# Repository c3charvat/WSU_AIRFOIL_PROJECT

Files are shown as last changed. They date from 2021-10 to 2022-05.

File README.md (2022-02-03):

# WRIGHT STATE DUAL AIRFOIL PROJECT
Source code for the WSU Dual Airfoil Senior Design project.
# Problem Statement:
Wright State graduate and undergraduate students would like to research\
the affects of dual airfoils on lift and pressure.\
The current set up for this system enables the user to set the angle\
of attack (AoA) on each of the airfoils as well as set gap and stagger between them.\
The gap and stagger motion is provided by electrical actuators moving on plastic \
linear berrings driven by a Texas Instruments DAQ. Programed in LabVIEW.\
The AoA was set manual via an arbitrary sharpy scale on a mental plate.

This presented three major issues:\
Year to year no one could actually program, or control this system.\
This system proved to be non-repeatable. (A fundemtal characteristic of an experiment)\
Friction / system stiffness of the linear berrings further reduced the repeatability.\
Using an arbitrary scale made the system qualitative.

# Key project objectives:
*Document all decisions, reasoning, choices, code and files for year to year use.\
*Enable repeatability with a resolution of .1mm gap and stagger and .05* AoA.\
*Use readily available parts to enable maintenance and keep the price down.

The function of this project is to drive 5 steppers in the desired modes.\
They are:\
LCD static- Motor move as soon as data is available from LCD\
LCD Trigger - Motors wait on a "go" button to be pressed in the LCD\
LCD W. Ext. T. - Motors wait on external physical trigger.\
Serial - motors move as soon as serial data is a available.\
Serial W. Ext. T. - Motors move on the press of an physical switch.

# Key features:
Custom G code implementation.\
Implemtiaton of Uart stepper control.\
Native 256 and interpolated 256 micro stepping capable.\
Selectable Spread Cycle or Silent Steptick enabled.\
Low cost use of a 3d printer motherboard.\
Written in Arduino for ease of use for non code centered users.\
PlatformIO configured with nessary libraries provided.\
(For year to year support of Senior design teams).\
(remember to change the path of the libraries in platform.ini)\
Full LCD implementation using SPI.\
Full System UI, with user input enabled through an encoder.\
Prosessor and IDE:\
ARM Stm32f446ZE Branch with Custom PlatformIO implantation.
Black magic probe debugging enabled.\

# Written by:
Collin C. Charvat\
charvat.3@wright.edu\
c3charvat@gmail.com\
B.S. Mechanical Engineering, Wright State University. 22'\
College of Engineering and Computer Science.

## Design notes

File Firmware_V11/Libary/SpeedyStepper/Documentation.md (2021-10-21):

# SpeedyStepper:

This Arduino library is used to control one or more stepper motors.  The motors are accelerated and decelerated as they travel to their destination.  The library has been optimized for speed.

##### Stepper Motor Driver Boards:

SpeedyStepper requires that your stepper motor be connected to the Arduino using drive electronics having a "Step and Direction" interface.  For a hookup guide, go to:
     https://github.com/Stan-Reifel/SpeedyStepper

Examples of Stepper Motor Driver Boards are:

  Pololu's DRV8825 Stepper Motor Driver Carrier:
      https://www.pololu.com/product/2133

  Pololu's A4988 Stepper Motor Driver Carrier:
      https://www.pololu.com/product/2980

  Sparkfun's Big Easy Driver:
      https://www.sparkfun.com/products/12859

  GeckoDrive G203V industrial controller:
      https://www.geckodrive.com/g203v.html

For all driver boards, it is VERY important that you set the motor current.  This is typically done by adjusting a potentiometer on the board.  Read the driver board's documentation to learn how.

##### Selecting a power supply:

Stepper motors will spin with greatest torque at speed, when using a power supply voltage that is many times higher than the motor's voltage rating.  Don't worry about this, the current setting on the driver board keeps the motor protected.  I often use NEMA 17 motors with a voltage rating around 3V, then power my driver board with a 24V supply.  Just make sure that your power supply voltage does not exceed the voltage rating of the driver board.  12V motors with a 12V supply will have much lower torque than my 3V/24V combo.  (Note: NEMA 17 describes the size of the motor, 1.7 inches wide)

Smaller motors can typically spin faster than larger ones.  The best way to evaluate a motor is by looking at its "torque curve".  Most of the stepper motors sold by www.pololu.com have a data sheet on their website 
showing a torque curve (motors sold on Amazon usually do not).

##### Microsteps:

Most stepper motors have a 1.8 degree step angle, which results in 200 steps/revolution.  A typical *Stepper Motor Driver Board* allows you to configure it for Microstepping.  Microstepping gives you greater angular resolution and smoother rotates.  If your board is setup for 2x microstepping, then you will need to move 400 steps for one rotation.  Using 8x microstepping requires 1600 steps / revolution.

##### SpeedyStepper vs FlexyStepper:

A limitation of this library is that once a motion starts, you can not change the target position, speed or rate of acceleration until the motion has completed. The only exception to this is that you can issue a "Stop" at any point in time, which will cause the motor to decelerate to a stop.  The *FlexyStepper* library allows you to make changes in motion.  See:  https://github.com/Stan-Reifel/FlexyStepper

##### The advantage of SpeedyStepper:

Because this library doesn't allow making changes while moving, it can generate steps faster than FlexyStepper.  SpeedyStepper can generate a maximum of about 12,500 steps per second using an Arduino Uno.  Assuming a system driving only one motor at a time, no microstepping, using a 200 steps/rotation motor, the maximum speed is about 62 RPS or 3750 RPM (most stepper motor can not go this fast).  Driving one motor in half step mode, a maximum speed of 31 RPS or 1875 RPM can be reached.  In quarter step mode about 15 RPS or 937 RPM.  Running multiple motors at the same time will reduce the maximum speed.  For example running two motors will reduce the step rate by half or more.

##### Absolute vs relative moves:

The SpeedyStepper functions that make a motor move come in two flavors: *Absolute* and *Relative*.  Relative moves will use a coordinate system that is relative to the motor's current position.  For example moving relative 200 steps, then another 200, then another 200, will turn 600 steps in total (and end up at an absolute position of 600).

Absolute moves use a coordinate system that is referenced to the original position of the motor when it is first turned on.  First issuing an absolute move to position 200 will rotate forward one rotation.  Then running the next absolute move to position 400 will turn just one more revolution in the same direction.  Finally, an absolute move to position 0 will rotate backward two revolutions, back to the starting point.

##### Units of travel:

Frequently issuing move commands in units of "Steps" is not as intuitive as other units, such as *Millimeters* or *Rotations*.  Many stepper motors are used in projects where the motions are linear instead of rotational.  Examples are XY mechanisms such as plotters and 3D printers.  In these cases issuing move commands in Millimeters is much more intuitive than Steps. 

If you choose to work in units of Rotations, you will first need tell the library "how many steps makes one rotation".  Do so using the function:  *setStepsPerRevolution()*.  Then move the motor with calls to *moveToPositionInRevolutions()*  and  *moveRelativeInRevolutions()*.

If you choose to work in units of Millimeters, you will need tell the library "how many steps makes one millimeter".  Do so using the function:  *setStepsPerMillimeter()*.  Then move the motor with calls to *moveToPositionInMillimeters()*  and  *moveRelativeInMillimeters()*.

##### Blocking vs Non-blocking function calls:

The easiest way to tell a stepper motor to move is using a function like this:
	moveToPositionInSteps(125)

This function will rotate the motor until it gets to coordinate 125, but the function call doesn't return until the motion is complete.  This is a *Blocking* function.

Blocking functions are a limitation if you want to do other things while the motor is running.  Examples of "other things" might be to:  1) Run two motors at once.  2) Check if a button is press, then decelerate to a stop.  3) Turn on a solenoid when the motor moves past position 850.  4) Flash a strobe every 200 steps.  5) Run continuously as long as a temperature is below 125 degrees.  To do these types of things *Non-blocking* functions are used.  Here is an example:

```
  //
  // setup the motor so that it will rotate 2000 steps, note: this 
  // command does not start moving yet
  //
  stepper.setupMoveInSteps(2000);
  
  //
  // now execute the move, looping until the motor has finished
  //
  while(!stepper.motionComplete())
  {
    stepper.processMovement();       // this call moves themotor
    
    //
    // check if motor has moved past position 400, if so turn On the LED
    //
    if (stepper.getCurrentPositionInSteps() == 400)
      digitalWrite(LED_PIN, HIGH);
  }
```

There are some limitations to consider:

1. The code that you run while the stepper is moving needs to execute VERY fast.  Perhaps no longer than 0.05 milliseconds.  
2. The only change that you can make to a motion once it starts moving is to decelerate to a stop using *setupStop()*.  Note: This library does not allow changing the target position or speed while the motor is moving.  (You CAN make these changes in FlexyStepper library.

##### Homing:

Many stepper motor projects need to move to exact positions.  This usually requires that the stepper motor library knows where the motor is before it makes its first move.  To achieve this automatically, you will use a 
*Limit Switch* that is pressed by the mechanism when the motor moves all-the-way to one end of its travel.  This procedure called *Homing*, is executed when power is first applied.  A homing program moves the motor toward the limit switch until the switch is pressed, then resets the library so that the motor is now at position 0.

Home automatically is easily done using one of these functions:

- moveToHomeInSteps()
- moveToHomeInRevolutions()
- moveToHomeInMillimeters()

### Usage examples:

```
Near the top of the program, add:
    include "SpeedyStepper.h"

For each stepper, declare a global object outside of all functions as follows:
    SpeedyStepper stepper1;
    SpeedyStepper stepper2;

In Setup(), assign IO pins used for Step and Direction:
    stepper1.connectToPins(10, 11);
    stepper2.connectToPins(12, 14);
```

    Move one motor in units of steps:
        //
        // set the speed in steps/second and acceleration in steps/second/second
        //
        stepper1.setSpeedInStepsPerSecond(100);
        stepper1.setAccelerationInStepsPerSecondPerSecond(100);
    
        //
        // move 200 steps in the backward direction
        //
        stepper1.moveRelativeInSteps(-200);
    
        //
        // move to an absolute position of 200 steps
        //
        stepper1.moveToPositionInSteps(200);

    Move one motor in units of revolutions:
        //
        // set the number of steps per revolutions, 200 with no microstepping, 
        // 800 with 4x microstepping
        //
        stepper1.setStepsPerRevolution(200);
    
        //
        // set the speed in rotations/second and acceleration in 
        // rotations/second/second
        //
        stepper1.setSpeedInRevolutionsPerSecond(1);
        stepper1.setAccelerationInRevolutionsPerSecondPerSecond(1);
    
        //
        // move backward 1.5 revolutions
        //
        stepper1.moveRelativeInRevolutions(-1.5);
    
        //
        // move to an absolute position of 3.75 revolutions
        //
        stepper1.moveToPositionInRevolutions(3.75);

    Move one motor in units of millimeters:
        //
        // set the number of steps per millimeter
        //
        stepper1.setStepsPerMillimeter(25);
    
        //
        // set the speed in millimeters/second and acceleration in 
        // millimeters/second/second
        //
        stepper1.setSpeedInMillimetersPerSecond(20);
        stepper1.setAccelerationInMillimetersPerSecondPerSecond(20);
    
        //
        // move backward 15.5 millimeters
        //
        stepper1.moveRelativeInMillimeters(-15.5);
    
        //
        // move to an absolute position of 125 millimeters
        //
        stepper1.moveToPositionInMillimeters(125);

    Move two motors in units of revolutions:
        //
        // set the number of steps per revolutions, 200 with no microstepping, 
        // 800 with 4x microstepping
        //
        stepper1.setStepsPerRevolution(200);
        stepper2.setStepsPerRevolution(200);
    
        //
        // set the speed in rotations/second and acceleration in 
        // rotations/second/second
        //
        stepper1.setSpeedInRevolutionsPerSecond(1);
        stepper1.setAccelerationInRevolutionsPerSecondPerSecond(1);
        stepper2.setSpeedInRevolutionsPerSecond(1);
        stepper2.setAccelerationInRevolutionsPerSecondPerSecond(1);
    
        //
        // setup motor 1 to move backward 1.5 revolutions, this step does not 
        // actually move the motor
        //
        stepper1.setupRelativeMoveInRevolutions(-1.5);
    
        //
        // setup motor 2 to move forward 3.0 revolutions, this step does not 
        // actually move the motor
        //
        stepper2.setupRelativeMoveInRevolutions(3.0);
    
        //
        // execute the moves
        //
        while((!stepper1.motionComplete()) || (!stepper2.motionComplete()))
        {
          stepper1.processMovement();
          stepper2.processMovement();
        }

# The library of functions  

### Setup functions: 

```
//
// connect the stepper object to the IO pins
//  Enter:  stepPinNumber = IO pin number for the Step
//          directionPinNumber = IO pin number for the direction bit
//          enablePinNumber = IO pin number for the enable bit (LOW is enabled)
//            set to 0 if enable is not supported
//
void connectToPins(byte stepPinNumber, byte directionPinNumber)
```

### Functions with units in millimeters: 

```
//
// set the number of steps the motor has per millimeter
//
void setStepsPerMillimeter(float motorStepPerMillimeter)

//
// get the current position of the motor in millimeter, this functions is updated
// while the motor moves
//  Exit:  a signed motor position in millimeter returned
//
float getCurrentPositionInMillimeters()

//
// set current position of the motor in millimeter, this does not move the motor
//
void setCurrentPositionInMillimeters(float currentPositionInMillimeter)

//
// set the maximum speed, units in millimeters/second, this is the maximum speed  
// reached while accelerating
// Note: this can only be called when the motor is stopped
//  Enter:  speedInMillimetersPerSecond = speed to accelerate up to, units in 
//          millimeters/second
//
void setSpeedInMillimetersPerSecond(float speedInMillimetersPerSecond)

//
// set the rate of acceleration, units in millimeters/second/second
// Note: this can only be called when the motor is stopped
//  Enter:  accelerationInMillimetersPerSecondPerSecond = rate of acceleration,  
//          units in millimeters/second/second
//
void setAccelerationInMillimetersPerSecondPerSecond(
                      float accelerationInMillimetersPerSecondPerSecond)

//
// home the motor by moving until the homing sensor is activated, then set the  
// position to zero, with units in millimeters
//  Enter:  directionTowardHome = 1 to move in a positive direction, -1 to move in 
//             a negative directions 
//          speedInMillimetersPerSecond = speed to accelerate up to while moving 
//             toward home, units in millimeters/second
//          maxDistanceToMoveInMillimeters = unsigned maximum distance to move 
//             toward home before giving up
//          homeSwitchPin = pin number of the home switch, switch should be 
//             configured to go low when at home
//  Exit:   true returned if successful, else false
//
bool moveToHomeInMillimeters(long directionTowardHome,  
  float speedInMillimetersPerSecond, long maxDistanceToMoveInMillimeters, 
  int homeLimitSwitchPin)

//
// move relative to the current position, units are in millimeters, this function  
// does not return until the move is complete
//  Enter:  distanceToMoveInMillimeters = signed distance to move relative to the  
//          current position in millimeters
//
void moveRelativeInMillimeters(float distanceToMoveInMillimeters)

//
// setup a move relative to the current position, units are in millimeters, no   
// motion occurs until processMove() is called
// Note: this can only be called when the motor is stopped
//  Enter:  distanceToMoveInMillimeters = signed distance to move relative to the  
//            currentposition in millimeters
//
void setupRelativeMoveInMillimeters(float distanceToMoveInMillimeters)

//
// move to the given absolute position, units are in millimeters, this function 
// does not return until the move is complete
//  Enter:  absolutePositionToMoveToInMillimeters = signed absolute position to 
//            move toin units of millimeters
//
void moveToPositionInMillimeters(
                      float absolutePositionToMoveToInMillimeters)

//
// setup a move, units are in millimeters, no motion occurs until processMove() is 
// called.  Note: this can only be called when the motor is stopped
//  Enter:  absolutePositionToMoveToInMillimeters = signed absolute position to move  
//          to in units of millimeters
//
void setupMoveInMillimeters(
                      float absolutePositionToMoveToInMillimeters)

//
// Get the current velocity of the motor in millimeters/second.  This functions is 
// updated while it accelerates up and down in speed.  This is not the desired  
// speed, but the speed the motor should be moving at the time the function is   
// called.  This is a signed value and is negative when motor is moving backwards.
// Note: This speed will be incorrect if the desired velocity is set faster than
// this library can generate steps, or if the load on the motor is too great for
// the amount of torque that it can generate.
//  Exit:  velocity speed in millimeters per second returned, signed
//
float getCurrentVelocityInMillimetersPerSecond()

```

### Functions with units in revolutions: 

```
//
// set the number of steps the motor has per revolution
//
void setStepsPerRevolution(float motorStepPerRevolution)

//
// get the current position of the motor in revolutions, this functions is updated
// while the motor moves
//  Exit:  a signed motor position in revolutions returned
//
float getCurrentPositionInRevolutions()

//
// set current position of the motor in revolutions, this does not move the motor
//
void setCurrentPositionInRevolutions(
   float currentPositionInRevolutions)

//
// set the maximum speed, units in revolutions/second, this is the maximum speed  
// reached while accelerating.  Note: this can only be called when the motor is 
// stopped
//  Enter:  speedInRevolutionsPerSecond = speed to accelerate up to, units in 
//            revolutions/second
//
void setSpeedInRevolutionsPerSecond(float speedInRevolutionsPerSecond)

//
// set the rate of acceleration, units in revolutions/second/second
// Note: this can only be called when the motor is stopped
//  Enter:  accelerationInRevolutionsPerSecondPerSecond = rate of acceleration,  
//            units inrevolutions/second/second
//
void setAccelerationInRevolutionsPerSecondPerSecond(
                      float accelerationInRevolutionsPerSecondPerSecond)

//
// home the motor by moving until the homing sensor is activated, then set the  
// position to zero, with units in revolutions
//  Enter:  directionTowardHome = 1 to move in a positive direction, -1 to move in 
//             a negative directions 
//          speedInRevolutionsPerSecond = speed to accelerate up to while moving 
//             toward home, units in revolutions/second
//          maxDistanceToMoveInRevolutions = unsigned maximum distance to move 
//             toward home before giving up
//          homeSwitchPin = pin number of the home switch, switch should be 
//             configured to go low when at home
//  Exit:   true returned if successful, else false
//
bool moveToHomeInRevolutions(long directionTowardHome, 
  float speedInRevolutionsPerSecond, long maxDistanceToMoveInRevolutions, 
  int homeLimitSwitchPin)

//
// move relative to the current position, units are in revolutions, this function  
// does not return until the move is complete
//  Enter:  distanceToMoveInRevolutions = signed distance to move relative to the  
//          current position in revolutions
//
void moveRelativeInRevolutions(float distanceToMoveInRevolutions)

//
// setup a move relative to the current position, units are in revolutions, no   
// motion occurs until processMove() is called.  Note: this can only be called 
// when the motor is stopped
//  Enter:  distanceToMoveInRevolutions = signed distance to move relative to the  
//          current position in revolutions
//
void setupRelativeMoveInRevolutions(float distanceToMoveInRevolutions)

//
// move to the given absolute position, units are in revolutions, this function 
// does not return until the move is complete
//  Enter:  absolutePositionToMoveToInRevolutions = signed absolute position to  
//          move to in units of revolutions
//
void moveToPositionInRevolutions(
       float absolutePositionToMoveToInRevolutions)

//
// setup a move, units are in revolutions, no motion occurs until processMove() is 
// called.  Note: this can only be called when the motor is stopped
//  Enter:  absolutePositionToMoveToInRevolutions = signed absolute position to  
//          move to inunits of revolutions
//
void setupMoveInRevolutions(
          float absolutePositionToMoveToInRevolutions)

//
// Get the current velocity of the motor in revolutions/second.  This functions is 
// updated while it accelerates up and down in speed.  This is not the desired  
// speed, but the speed the motor should be moving at the time the function is   
// called.  This is a signed value and is negative when motor is moving backwards.
// Note: This speed will be incorrect if the desired velocity is set faster than
// this library can generate steps, or if the load on the motor is too great for
// the amount of torque that it can generate.
//  Exit:  velocity speed in revolutions per second returned, signed
//
float getCurrentVelocityInRevolutionsPerSecond()

```

### Functions with units in steps: 

```
//
// set the current position of the motor in steps, this does not move the motor
// Note: This function should only be called when the motor is stopped
//    Enter:  currentPositionInSteps = the new position of the motor in steps
//
void setCurrentPositionInSteps(long currentPositionInSteps)

//
// get the current position of the motor in steps, this functions is updated
// while the motor moves
//  Exit:  a signed motor position in steps returned
//
long getCurrentPositionInSteps()

//
// setup a "Stop" to begin the process of decelerating from the current velocity to  
// zero, decelerating requires calls to processMove() until the move is complete
// Note: This function can be used to stop a motion initiated in units of steps or 
// revolutions
//
void setupStop()

//
// set the maximum speed, units in steps/second, this is the maximum speed reached  
// while accelerating
// Note: this can only be called when the motor is stopped
//  Enter:  speedInStepsPerSecond = speed to accelerate up to, units in steps/second
//
void setSpeedInStepsPerSecond(float speedInStepsPerSecond)

//
// set the rate of acceleration, units in steps/second/second
// Note: this can only be called when the motor is stopped
//  Enter:  accelerationInStepsPerSecondPerSecond = rate of acceleration, units in 
//          steps/second/second
//
void setAccelerationInStepsPerSecondPerSecond(
                      float accelerationInStepsPerSecondPerSecond)

//
// home the motor by moving until the homing sensor is activated, then set the 
// position to zero with units in steps
//  Enter:  directionTowardHome = 1 to move in a positive direction, -1 to move in 
//             a negative directions 
//          speedInStepsPerSecond = speed to accelerate up to while moving toward 
//             home, units in steps/second
//          maxDistanceToMoveInSteps = unsigned maximum distance to move toward 
//             home before giving up
//          homeSwitchPin = pin number of the home switch, switch should be 
//             configured to go low when at home
//  Exit:   true returned if successful, else false
//
bool moveToHomeInSteps(long directionTowardHome, 
  float speedInStepsPerSecond, long maxDistanceToMoveInSteps, int homeLimitSwitchPin)

//
// move relative to the current position, units are in steps, this function does 
// not return until the move is complete
//  Enter:  distanceToMoveInSteps = signed distance to move relative to the current 
//            position in steps
//
void moveRelativeInSteps(long distanceToMoveInSteps)

//
// setup a move relative to the current position, units are in steps, no motion  
// occurs until processMove() is called.  Note: this can only be called when the 
// motor is stopped
//  Enter:  distanceToMoveInSteps = signed distance to move relative to the current  
//          position in steps
//
void setupRelativeMoveInSteps(long distanceToMoveInSteps)

//
// move to the given absolute position, units are in steps, this function does not 
// return until the move is complete
//  Enter:  absolutePositionToMoveToInSteps = signed absolute position to move to  
//            in units of steps
//
void moveToPositionInSteps(long absolutePositionToMoveToInSteps)

//
// setup a move, units are in steps, no motion occurs until processMove() is called
// Note: this can only be called when the motor is stopped
//  Enter:  absolutePositionToMoveToInSteps = signed absolute position to move to in 
//          units of steps
//
void setupMoveInSteps(long absolutePositionToMoveToInSteps)

//
// if it is time, move one step
//  Exit:  true returned if movement complete, false returned not a final target 
//           position yet
//
bool processMovement(void)

//
// Get the current velocity of the motor in steps/second.  This functions is updated
// while it accelerates up and down in speed.  This is not the desired speed, but  
// the speed the motor should be moving at the time the function is called.  This  
// is a signed value and is negative when the motor is moving backwards.
// Note: This speed will be incorrect if the desired velocity is set faster than
// this library can generate steps, or if the load on the motor is too great for
// the amount of torque that it can generate.
//  Exit:  velocity speed in steps per second returned, signed
//
float getCurrentVelocityInStepsPerSecond()

//
// check if the motor has competed its move to the target position
//  Exit:  true returned if the stepper is at the target position
//
bool motionComplete()

```

Copyright (c) 2018 S. Reifel & Co.  -   Licensed under the MIT license.

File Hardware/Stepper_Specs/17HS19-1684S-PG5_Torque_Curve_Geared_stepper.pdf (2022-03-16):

## MAX. Permissible Torque：2Nm

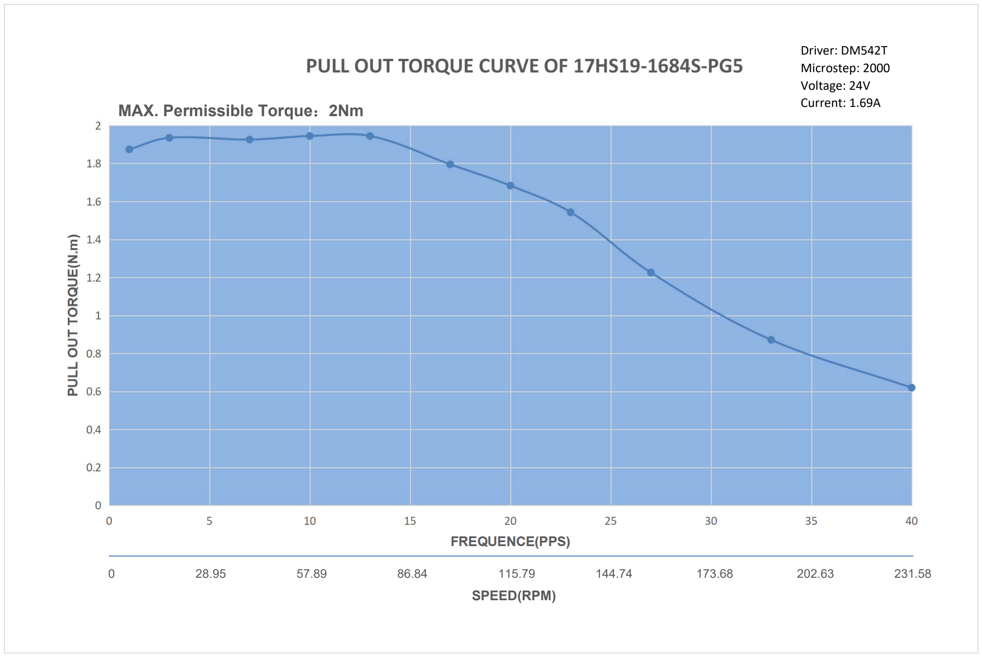
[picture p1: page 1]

SPEED(RPM)

0 | 28.95 | 57.89 | 86.84 | 115.79 | 144.74 | 173.68 | 202.63 | 231.58

Driver: DM542T
Microstep: 2000
Voltage: 24V
Current: 1.69A

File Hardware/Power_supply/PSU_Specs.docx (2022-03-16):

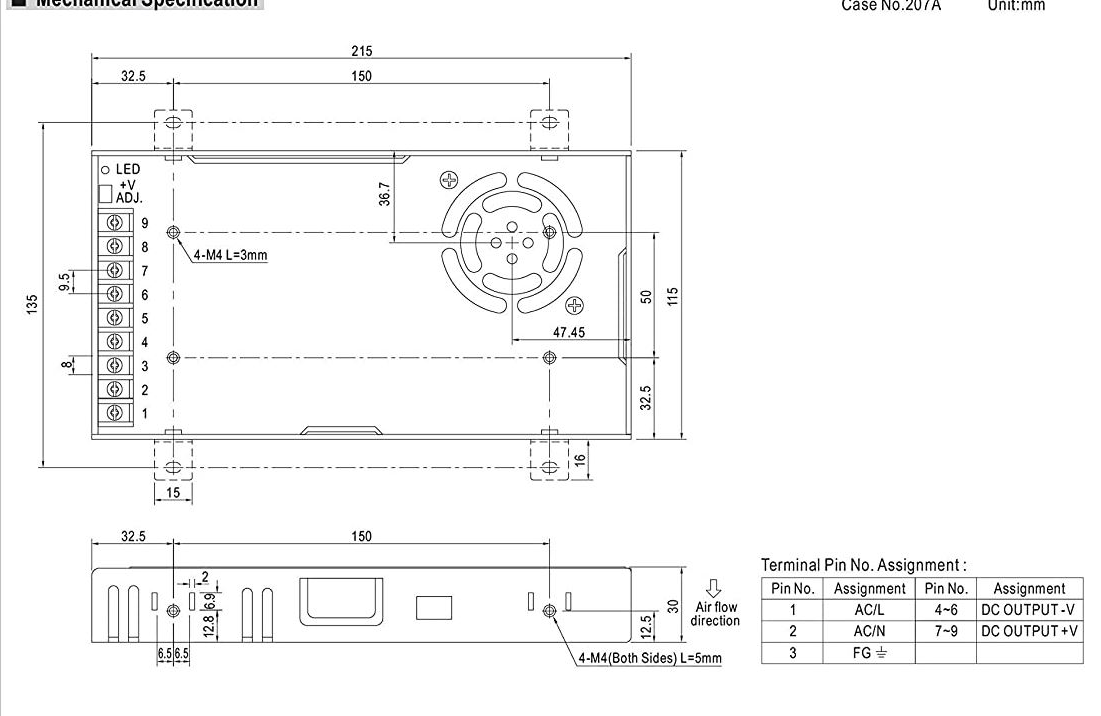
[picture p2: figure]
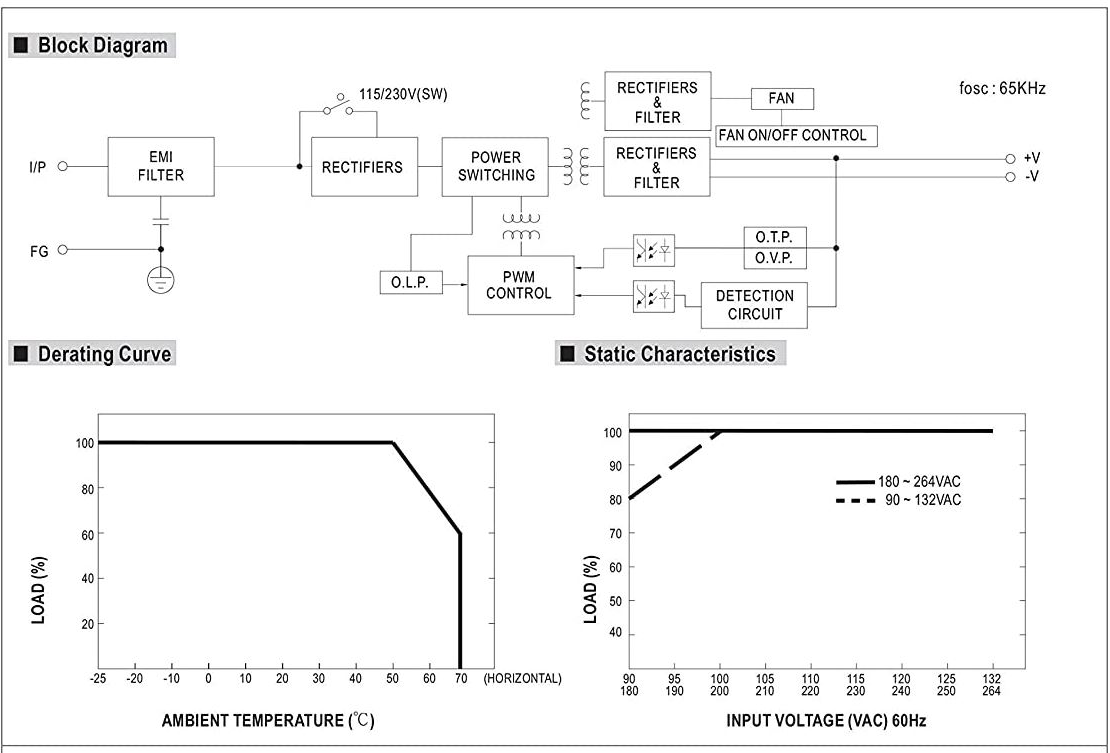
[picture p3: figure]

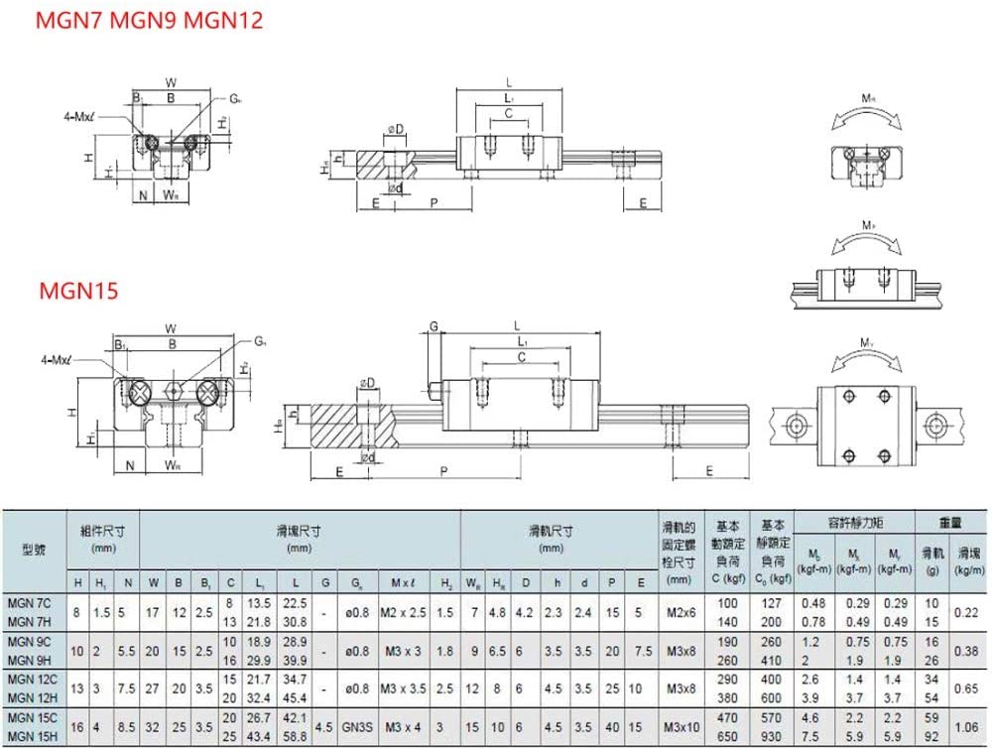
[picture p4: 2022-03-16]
Hardware/Linear_rails/61ZwrpNV6dL._AC_SL1000_.jpg

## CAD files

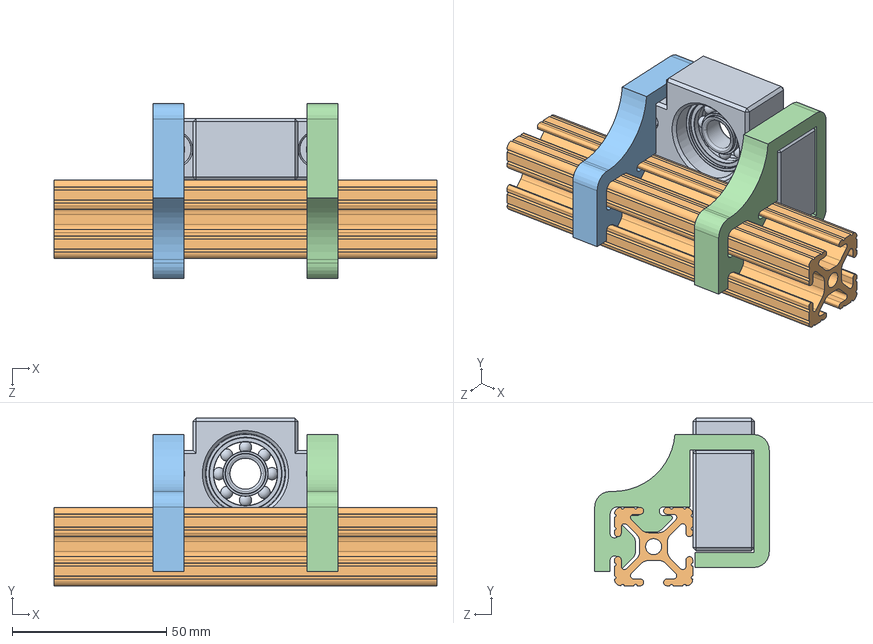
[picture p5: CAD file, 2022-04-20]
CADD/Dual Airfoil/Frame/bf12_to_tslot/bf12_to_tslot_sub_assm.SLDASM
124.2 x 54.4 x 56.6 mm
BF12
47065T121_T-Slotted Framing
bf12_to_tslot_V2_left
bf12_to_tslot_V2_right

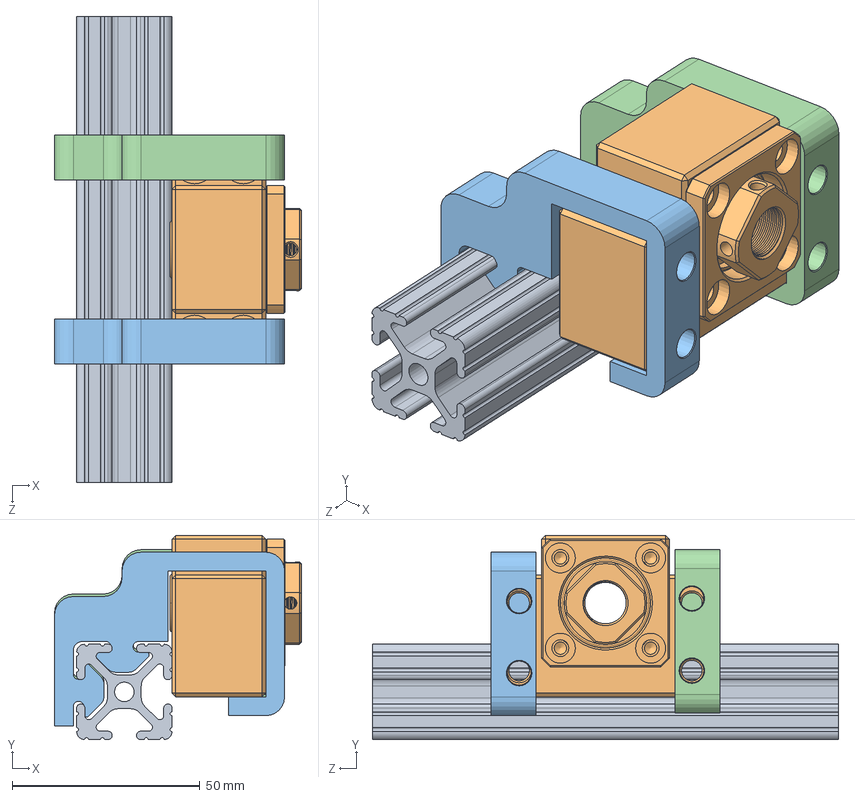
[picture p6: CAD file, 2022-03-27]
CADD/Dual Airfoil/Frame/bk12_to_tslot/bk12_t0_tslot.SLDASM
65.8 x 54.4 x 124.2 mm
47065T121_T-Slotted Framing
BK12
bk12_to_tslot_V1_mirriored
bk12_to_tslot_V1

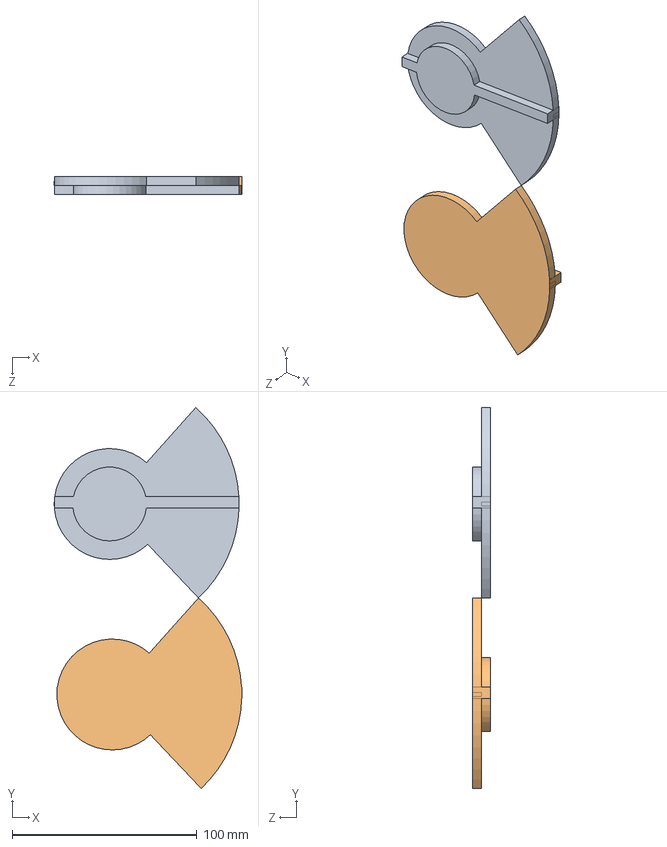
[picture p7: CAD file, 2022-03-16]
CADD/Dual Airfoil/Frame/AoA Slider/Black Plate Alignment.SLDASM
101.5 x 206.2 x 10.0 mm
black plate gap
black plate stagger

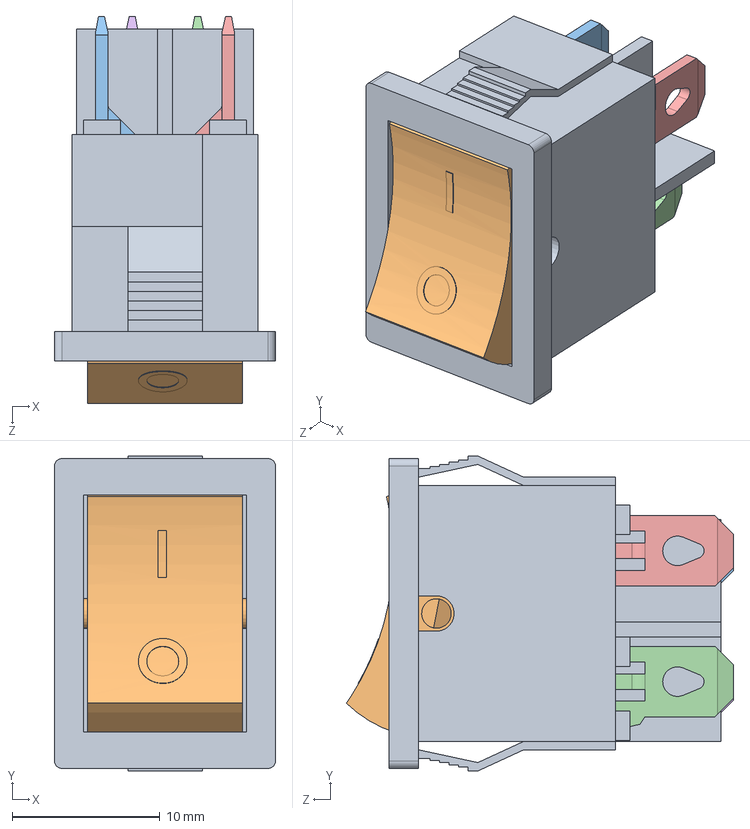
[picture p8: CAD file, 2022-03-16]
CADD/Dual Airfoil/Enclosure_assm/Power_socket/IEC320 C14 Inlet Power Module/switch.SLDASM
14.9 x 21.3 x 26.2 mm
switch_base
rocker
sm_tab_type1a
sm_tab_type1b
sm_tab_type2a
sm_tab_type2b

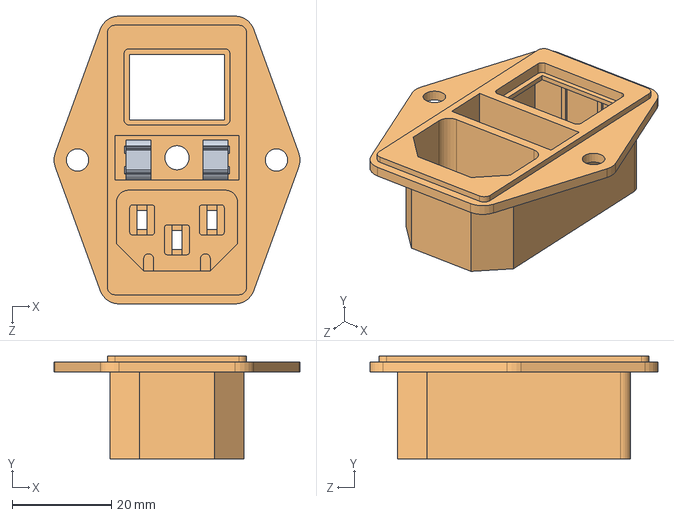
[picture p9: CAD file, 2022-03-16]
CADD/Dual Airfoil/Enclosure_assm/Power_socket/IEC320 C14 Inlet Power Module/IEC320-C14 .SLDASM
49.4 x 20.7 x 57.9 mm
fuse_clip_set
ilpm_case

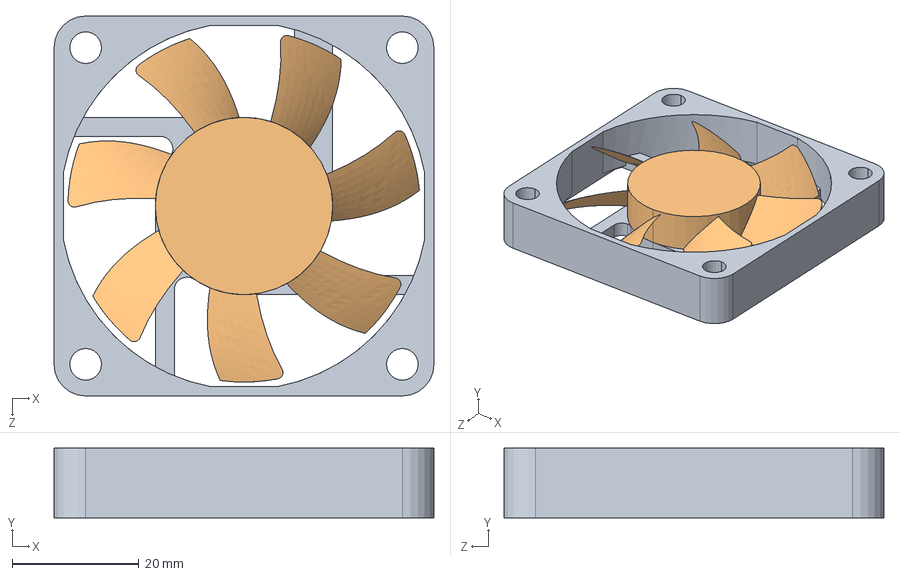
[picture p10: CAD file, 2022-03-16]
CADD/Dual Airfoil/Enclosure_assm/Fan_Assembly.STEP.SLDASM
60.0 x 11.0 x 60.0 mm
Fan_Case___ _________.STEP
Fan___ _________.STEP

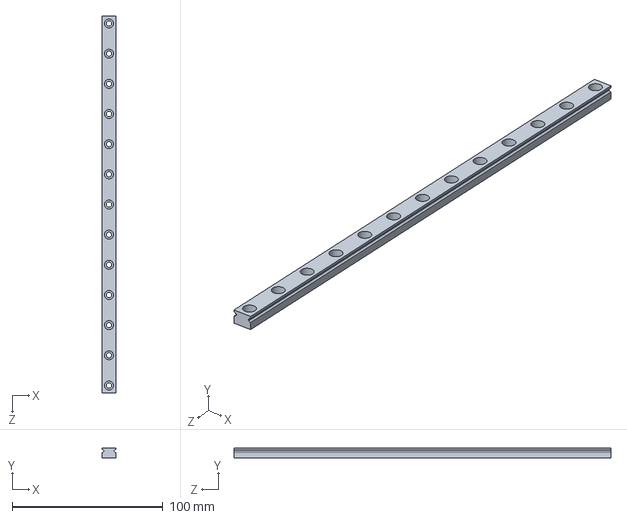
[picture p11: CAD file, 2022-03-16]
CADD/Dual Airfoil/Frame/MGN9.SLDASM
9.00 x 6.50 x 250.0 mm

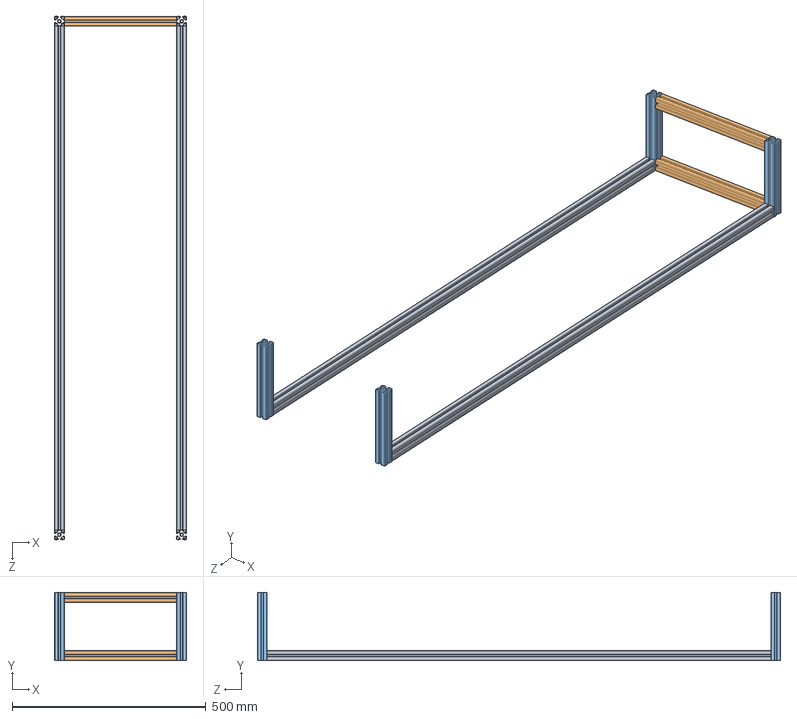
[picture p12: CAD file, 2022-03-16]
CADD/Dual Airfoil/Frame/Stagger Frame.SLDASM
340.8 x 175.8 x 1350.8 mm
Stagger - 1300x x 2
Gap-220z x 2
Stagger 125y x 4

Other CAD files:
CADD/Dual Airfoil/Enclosure_assm/motherboard bs/SIDE_L-1.stp.SLDASM
CADD/Dual Airfoil/Enclosure_assm/motherboard bs/C10.stp.STEP.SLDASM
CADD/Dual Airfoil/Enclosure_assm/motherboard bs/SOT23-5.stp.STEP.SLDASM
CADD/Dual Airfoil/Enclosure_assm/motherboard bs/254-3X4-1.stp.STEP.SLDASM
CADD/Dual Airfoil/Enclosure_assm/motherboard bs/R7.stp.SLDASM
CADD/Dual Airfoil/Enclosure_assm/motherboard bs/2P-254.stp.STEP.SLDASM
CADD/Dual Airfoil/Enclosure_assm/motherboard bs/TSSOP-16.stp.STEP.SLDASM
CADD/Dual Airfoil/Enclosure_assm/motherboard bs/Free-Models.stp.STEP.SLDASM
CADD/Dual Airfoil/Enclosure_assm/motherboard bs/User Library-V0603HD.stp.STEP.SLDASM
CADD/Dual Airfoil/Enclosure_assm/motherboard bs/C5.stp.STEP.SLDASM
CADD/Dual Airfoil/Enclosure_assm/Assem1.SLDASM
CADD/Dual Airfoil/Enclosure_assm/BIGTREETECH Octopus V1.0.stp.SLDASM
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

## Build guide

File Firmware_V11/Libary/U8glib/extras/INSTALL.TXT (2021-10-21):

U8GLIB
http://code.google.com/p/u8glib/

Install instructions for the Arduino environment.

  1. Start Arduino IDE
  2. In the Arduino IDE, import the library from the "Add Library" Menu.

Alternative install instructions for the Arduino environment.

  1. Unzip u8glib_arduino_vX.XX.zip into the "libraries" folder of the
      Arduino install directory
  2. Start Arduino IDE

Install instructions for the Chipkit (Arduino) environment.

  1. cd <mpide-... path>/libraries
  2. unzip u8glib_arduino_vX.XX.zip
  3. cd <mpide-... path>///hardware/pic32/libraries
  4. again: u8glib_arduino_vX.XX.zip
  5. Open hardware/pic32/cores/pic32/Print.h
	  Remove line
	    #define BYTE 0
	  from the file, use PRINT_BYTE instead of BYTE.

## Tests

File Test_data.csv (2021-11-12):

 | x | y | AoA T | AoA B
Scenario0 | 200 | 50 | -10 | 10
Scenario1 | 100 | 60 | 10 | -10
Scenario2 | 0 | 200 | 20 | 15
Scenario3 | 300 | 400 | 10 | 3
Scenario4 | 500 | 500 | 5 | 7
Scenario5 | 10 | 100 | 3 | 10

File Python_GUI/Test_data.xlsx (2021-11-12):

 | Scenario1
x | 20
y | 30
AoA T | 40
AoA B | 200

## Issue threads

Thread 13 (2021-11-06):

Movement bug

c3charvat, 2021-11-06:
Steppers still move after Error message is dismissed.

c3charvat, 2021-11-12:
Fixed by merging the serial and LCD position input variables into one and initializing temp positions. Postion_Data Removed.

Closed 2021-11-12.

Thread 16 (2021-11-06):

Implemtiaton - Hardware reset via software trigger?

c3charvat, 2021-11-06:
Use the exposed software reset pin to reset the board at the request of software in the event of an unrecoverable error.

c3charvat, 2021-11-13:
Implemented <R> Command

Closed 2021-11-13.

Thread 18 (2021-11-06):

Implemtiaton of leadscrew math

c3charvat, 2021-11-06:
X and Y axis need math to go from steps to mm moved. Which is the value the user inputs.

c3charvat, 2021-11-13:
Done

Closed 2021-11-13.

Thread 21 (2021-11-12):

Implement Stop/ Reset

c3charvat, 2021-11-12:
Implement Stop/Reset
For the LCD and for the GUI
This includes:
New Menu for Reset in LCD
Implementing reset Function for the GUI
Adding the reset Function in the g code parser

c3charvat, 2021-11-13:
Done Just Cuts power to the board Via PBO jumped to reset and set high Whenever the <R> code is sent

c3charvat, 2022-02-03:
software reset now implemented with NVIC_SystemReset(). -> only happens during error state

Closed 2022-02-03.

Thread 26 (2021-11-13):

Add Reset To LCD Menus

c3charvat, 2021-11-13:

c3charvat, 2021-11-20:
Reset is going to be handled by a physical switch - Per Discussion on 11/18

Closed 2021-11-20.

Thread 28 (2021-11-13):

Calculate the max distance to home and update the values in the homing function

c3charvat, 2021-11-13:

c3charvat, 2021-11-20:
This function is being replaced entirely, as it only works on a single axis at a time which isnt a good use case for this application as multiple steppers are used per axis -> a new homing function has been written using the move function

Closed 2021-11-20.

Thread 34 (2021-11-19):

X axis not moving ->

c3charvat, 2021-11-19:
Could be the driver?

c3charvat, 2021-11-24:
X axis moved, today, but never stopped and just kept going in circles.

c3charvat, 2021-12-14:
it moves, was an internal issue with the python in the way the movement was calculated

Closed 2021-12-14.

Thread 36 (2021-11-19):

Re-assign Motor Functions so they make sense for the board

c3charvat, 2021-11-19:
motor 2 is doubled
and we need to decide on the assignment of motors

c3charvat, 2021-11-22:
This will be implemented later names are fine for now.

Closed 2021-11-22.

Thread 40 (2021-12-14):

Rewrite and unify all homing functions

c3charvat, 2021-12-14:
Homing functions are a classic example of when we should use a high priority ISR (interrupt) and previously we had been using overloaded variables.

c3charvat, 2021-12-25:
This is done- untested

Closed 2021-12-25.

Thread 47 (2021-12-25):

Reduce the final axis movement

c3charvat, 2021-12-25:
Limit the axis to 5mm less than their actual max to allow the homing function to move the axis forward before coming back regardless of the state of the axis.
I.E if the axis was at the "max" it can move forward still then move back.

c3charvat, 2021-12-25:
This needs to include the aoa steppers too

c3charvat, 2022-02-03:
This needs the frame finished

c3charvat, 2022-04-20:
fixed in homing fix

Closed 2022-04-20.

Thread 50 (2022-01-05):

Homing function gpio issues

c3charvat, 2022-01-05:
https://github.com/stm32duino/Arduino_Core_STM32/issues/1005

For simplisty and function rewrite the function like in the link above

c3charvat, 2022-01-05:
untested-> implemented

c3charvat, 2022-02-03:
SpeedyStepper homing functions did not work with normally high stepper. I used part of the mbed/Cmsis core LL_gipo to directly manipulate the registers and an ISR routine to hold off the stepper when the limit switch is engaged. -> tested working 2/2/22

Closed 2022-02-03.

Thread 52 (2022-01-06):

Power cycle error state

c3charvat, 2022-01-06:
E stop pressed- doesn't kill the boards memory instantly. Causing the potential for unexpected movement.

c3charvat, 2022-02-03:
not sure this is truly an issue with the ac to dc relay.

Closed 2022-02-03.

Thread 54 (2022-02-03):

motor 3 is supposed to be an aoa stepper but moves like a y axis

c3charvat, 2022-02-03:

c3charvat, 2022-02-03:
fixed-> motor 4 was being treated as the AoA when it was a y axis motor. fixed motor 5 so it behaves as it should.

Closed 2022-02-03.

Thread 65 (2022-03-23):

Enable_Y_endstops

c3charvat, 2022-03-23:

c3charvat, 2022-03-27:
This is setting fixes with the homing fuctions

c3charvat, 2022-03-27:
all of them are enabled.. not tested

Closed 2022-03-27.

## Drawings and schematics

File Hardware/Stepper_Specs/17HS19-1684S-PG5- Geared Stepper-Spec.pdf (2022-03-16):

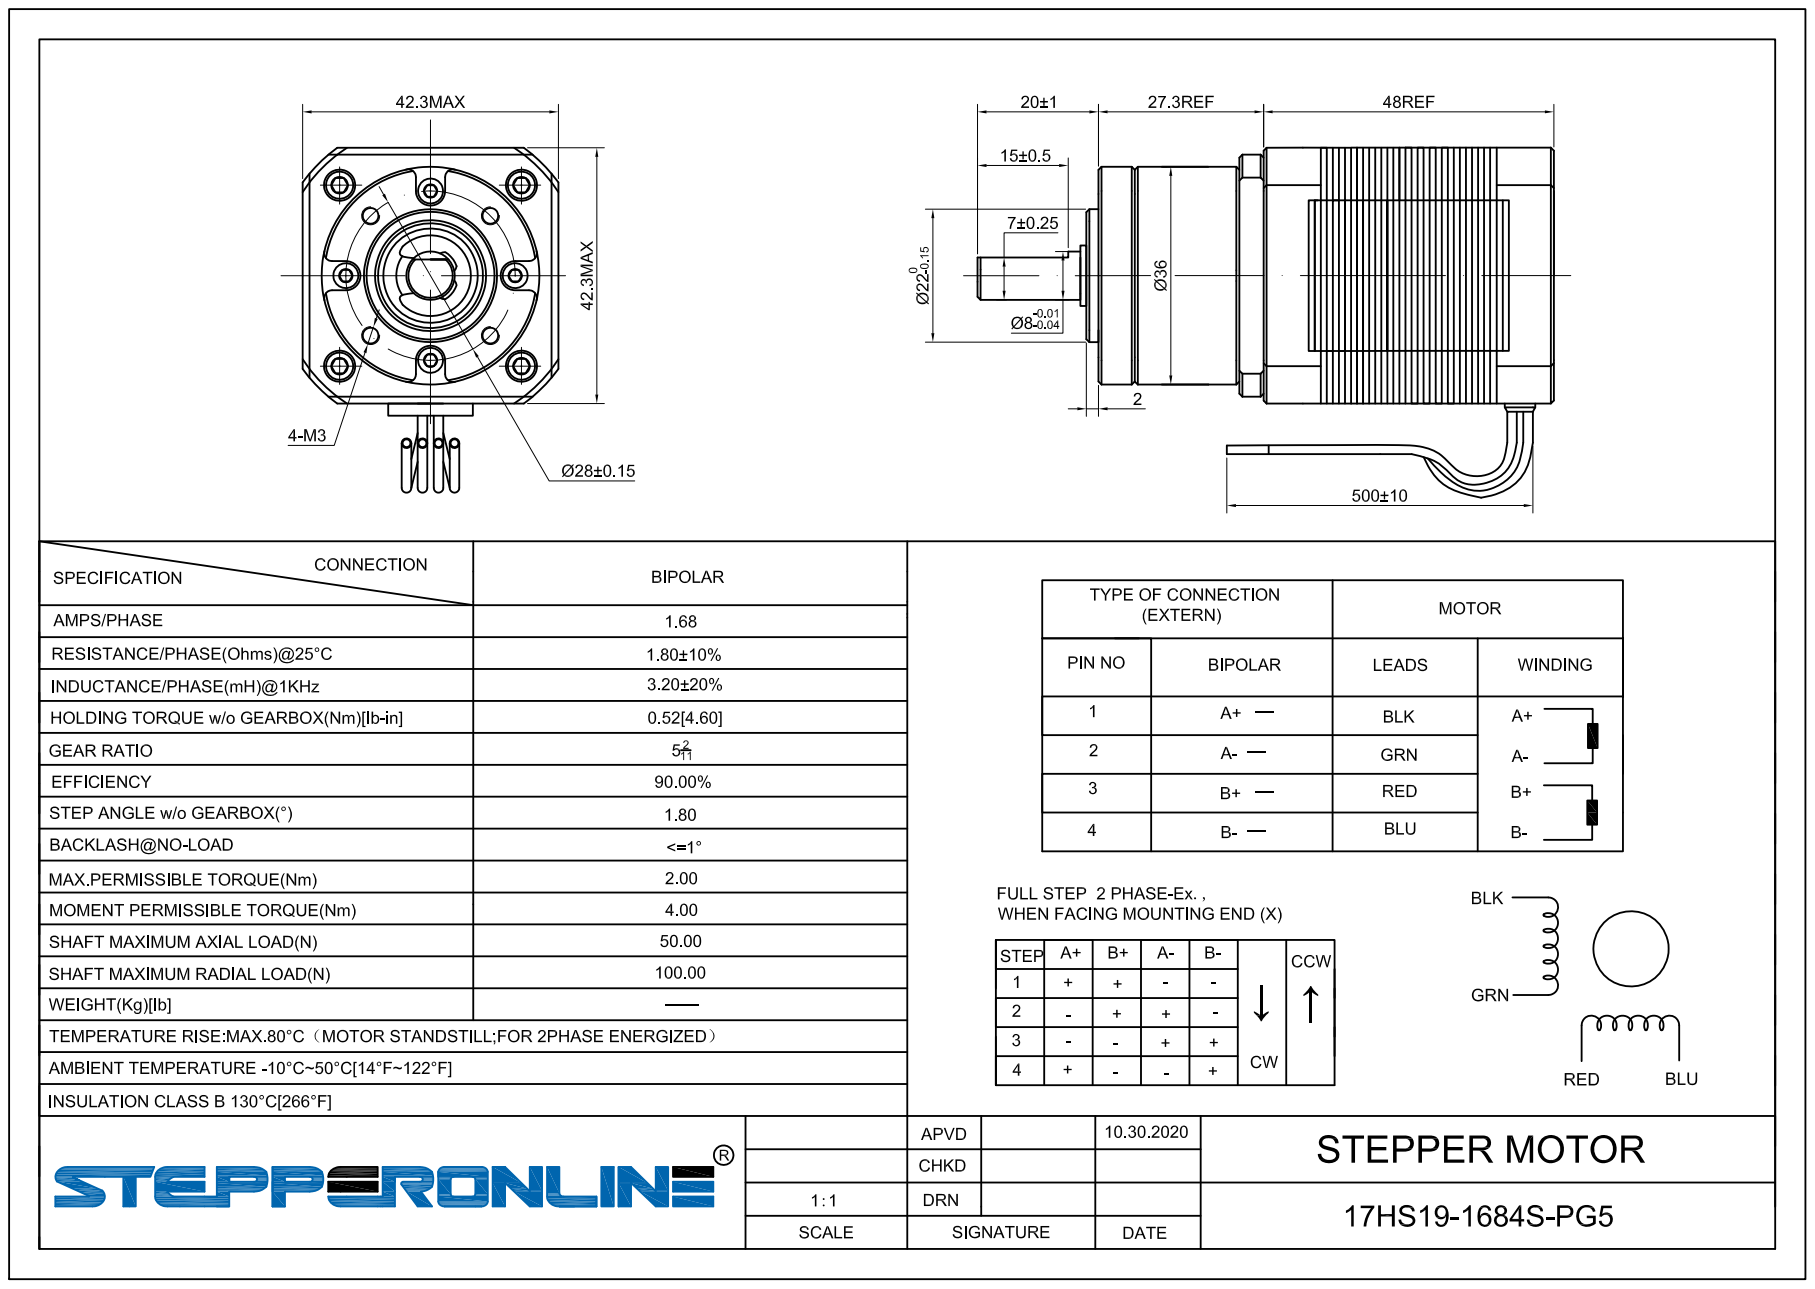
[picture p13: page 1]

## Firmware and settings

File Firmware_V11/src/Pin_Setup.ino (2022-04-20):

#include <Arduino.h>
#include <SpeedyStepper.h>

/* 
This file sets up the Pin Modes
It its important to note that Stepper driver 7 shares pins with the swd interface... 
So if you are not programming with dfu mode nothing will actuall program and wverthing ill result in errors
The SwD interface will not work untill a full power off and the SwD pins have been freed from any use in code. 
 https://www.st.com/resource/en/application_note/cd00167594-stm32-microcontroller-system-memory-boot-mode-stmicroelectronics.pdf
 Page 54 for more information
*/
int BUTTON = PE7; // encoder click on Creality Melzi screen
int BEEPER = PE8; // factory beeper on Creality Melzi screen
int ENCODER_RT = PE9; // left turn on the encoder 
int ENCODER_LT = PE12; // Right trun on the encoder
// Motor 0
const int MOTOR0_STEP_PIN = PF13 ;  // X axis X motion
const int MOTOR0_DIRECTION_PIN = PF12;  // X axis
const int MOTOR0_ENABLE = PF14;  // X axis
// Motor 1
const int MOTOR1_STEP_PIN = PG0;  // Y axis Y motion
const int MOTOR1_DIRECTION_PIN = PG1;  // Y axis
const int MOTOR1_ENABLE = PF15;  // Y axis
// Motor 2
const int MOTOR2_STEP_PIN = PF11;  // Z axis y motion
const int MOTOR2_DIRECTION_PIN = PG3;  // Z axis
const int MOTOR2_ENABLE = PG5;  // Z axis
// Motor 3
const int MOTOR3_STEP_PIN = PG4;  // E0 axis AoAt
const int MOTOR3_DIRECTION_PIN = PC1;  // E0 axis
const int MOTOR3_ENABLE = PA0;  // E0 axis;
// Motor 4
const int MOTOR4_STEP_PIN = PF9;  // e1 axis AoAB
const int MOTOR4_DIRECTION_PIN  = PF10;  // e1 axis // 
const int MOTOR4_ENABLE= PG2;  // e1 axis;
//Motor 5
const int MOTOR5_STEP_PIN = PC13;  // z axis
const int MOTOR5_DIRECTION_PIN  = PF0;  // z axis 
const int MOTOR5_ENABLE= PF1;  // z axis;
// Motor 6
const int MOTOR6_STEP_PIN = PE2;  // z axis 
const int MOTOR6_DIRECTION_PIN  = PE3;  // z axis 
const int MOTOR6_ENABLE= PD4;  // z axis;
// Motor 7
const int MOTOR7_STEP_PIN = PE6;  // z axis 
const int MOTOR7_DIRECTION_PIN  = PA14;  // z axis  // disabled for SWD programming 
const int MOTOR7_ENABLE= PE0;  // z axis;




void PIN_SETUP(){
// RESET
//pinMode(Reset,OUTPUT);
//digitalWrite(Reset,HIGH);

//X Stepper 
pinMode(MOTOR0_STEP_PIN, OUTPUT);
pinMode(MOTOR0_DIRECTION_PIN , OUTPUT);
pinMode(MOTOR0_ENABLE , OUTPUT);
// Y0 Stepper 
pinMode(MOTOR1_STEP_PIN, OUTPUT);
pinMode(MOTOR1_DIRECTION_PIN , OUTPUT);
pinMode(MOTOR1_ENABLE , OUTPUT);
// "Z" Y Stepper 1// Hardware Doubled
pinMode(MOTOR2_STEP_PIN, OUTPUT);
pinMode(MOTOR2_DIRECTION_PIN , OUTPUT);
pinMode(MOTOR2_ENABLE , OUTPUT);
// Y2 
pinMode(MOTOR3_STEP_PIN, OUTPUT);
pinMode(MOTOR3_DIRECTION_PIN , OUTPUT);
pinMode(MOTOR3_ENABLE , OUTPUT);
// A0A Top
pinMode(MOTOR4_STEP_PIN, OUTPUT);
pinMode(MOTOR4_DIRECTION_PIN, OUTPUT);
pinMode(MOTOR4_ENABLE, OUTPUT);
// AoA Bottom  
pinMode(MOTOR5_STEP_PIN, OUTPUT);
pinMode(MOTOR5_DIRECTION_PIN, OUTPUT);
pinMode(MOTOR5_ENABLE, OUTPUT);
// x2 Motor 
pinMode(MOTOR6_STEP_PIN, OUTPUT);
pinMode(MOTOR6_DIRECTION_PIN, OUTPUT);
pinMode(MOTOR6_ENABLE, OUTPUT);
// Y motor 4 
pinMode(MOTOR7_STEP_PIN, OUTPUT);
pinMode(MOTOR7_DIRECTION_PIN, OUTPUT);
pinMode(MOTOR7_ENABLE, OUTPUT);
// Limit Switches
pinMode(Motor0LimitSw, INPUT);
pinMode(Motor1LimitSw, INPUT);
pinMode(Motor2LimitSw, INPUT);
pinMode(Motor3LimitSw, INPUT);
pinMode(Motor4LimitSw, INPUT);
pinMode(Motor5LimitSw, INPUT);
pinMode(Motor6LimitSw, INPUT);
pinMode(Motor7LimitSw, INPUT);
// Extras 
// pinMode(4, OUTPUT); // Fan Pin Initilization 
pinMode(BEEPER, OUTPUT); // Beeper on LCD
pinMode(BUTTON, INPUT); // Encoder button
pinMode(ENCODER_RT, INPUT); // Encoder Move Direction
pinMode(ENCODER_LT, INPUT); // Encoder Move Direction
// Fan setup
const int Fan0 = PA8;
const int Fan1 = PE5;
const int Fan2 = PD12; 
pinMode(Fan0, OUTPUT);
pinMode(Fan1,OUTPUT);
pinMode(Fan2,OUTPUT);
digitalWrite(Fan0,HIGH);
digitalWrite(Fan1,HIGH);
digitalWrite(Fan2,HIGH);
/*
Fan 6 and 7 are on by default.
The remaining fan pins can be reused the top pin is hot as defined by the jumpers see pin diagram. 
*/
// Stepper Enables 
digitalWrite(MOTOR0_ENABLE , LOW); // Set the Enable Pin to Low to Enable the Driver 
digitalWrite(MOTOR1_ENABLE , LOW);
digitalWrite(MOTOR2_ENABLE , LOW);
digitalWrite(MOTOR3_ENABLE , LOW);
digitalWrite(MOTOR4_ENABLE , LOW);
digitalWrite(MOTOR5_ENABLE , LOW);
digitalWrite(MOTOR6_ENABLE , LOW); // Extras disabled for now
digitalWrite(MOTOR7_ENABLE , LOW);
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

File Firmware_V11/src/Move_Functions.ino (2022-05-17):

#include <Arduino.h>
// ~~~~~~~~~~~~~~~~~~~~~~~~~~~~~~~~~~~~~~~~~~~~~~~~~Movement Function ~~~~~~~~~~~~~~~~~~~~~~~~~~~~~~~~~~~~~~~~~~~~~~~~~~~~
//  "Static\n" 1
//  "LCD Trigger\n"2
//  "LCD External Trigger\n"3
//  "Serial Cont.\n" 4            // 2 and 4 are the exact same just moce togther as soon as you ge the command
//  "Serial Cont. Ext.T.\n"; 5        // 3 and 5 are the same
// const int Motor0LimitSw =PG6;
// const int Motor1LimitSw =PG12;
// const int Motor2LimitSw =PG9;
// const int Motor3LimitSw =PG13;
// const int Motor4LimitSw =PG10;
// const int Motor5LimitSw =PG14;
// const int Motor6LimitSw =PG11;
// const int Motor7LimitSw =PG15;

void MOVE_FUNCTION(void)
{                 // Selection =0
  movevar[0] = 0; // clear out any previous data that may or maynot have been canceled
  movevar[1] = 0;
  movevar[2] = 0;
  movevar[3] = 0;
  Serial.println("I got to \"MOVE_FUNCTION()\".");
  // Parse Out The Data into the correct move variable
  movevar[0] = ABS_POS(Xpos, 0);   // X Move
  movevar[1] = ABS_POS(Ypos, 1);   // Y and Z Move  // Pull Data From LCD MENU VARIBLES
  movevar[2] = ABS_POS(-1*(AoA[0]), 2); // E0 Move AoA Top
  movevar[3] = ABS_POS(-1*(AoA[1]), 3); // E1 Move AoA Bottom
  gui_output_function();           // return the stuff to the python the gui

  Serial.println("Motion_selection == 2 Com select == 2");
  // Normal Mode LCD
  Serial.println("Steps to move");
  Serial.println(movevar[0] * 6400);
  X_stepper.setupRelativeMoveInSteps(movevar[0]/5 *200*8); // Future: Make these iun terms of MM
  X2_stepper.setupRelativeMoveInSteps(movevar[0]/5 *200*8); // Future: Make these iun terms of MM
  Y0_stepper.setupRelativeMoveInSteps(movevar[1]/2 *200*8);
  Y1_stepper.setupRelativeMoveInSteps(movevar[1]/2 *200*8);
  Y2_stepper.setupRelativeMoveInSteps(movevar[1]/2 *200*8);
  Y3_stepper.setupRelativeMoveInSteps(movevar[1]/2 *200*8);
  AOAT_stepper.setupRelativeMoveInSteps(movevar[2]/1.8*5.18*8);
  AOAB_stepper.setupRelativeMoveInSteps(movevar[3]/1.8*5.18*8);
  // Call A Blocking Function that Stops the Machine from doing anything else while the stepper is moving  This is desired since we aren not updating mid move.
  Serial.println("Entering while loop");
  while ((!X_stepper.motionComplete()) || (!Y0_stepper.motionComplete()) || (!Y1_stepper.motionComplete()) || (!Y2_stepper.motionComplete()) ||(!Y3_stepper.motionComplete()) || (!AOAT_stepper.motionComplete()) || (!AOAB_stepper.motionComplete()))
  {
    X_stepper.processMovement();
    X2_stepper.processMovement();
    Y0_stepper.processMovement();
    Y1_stepper.processMovement(); // moving the Steppers here was a simple soltuion to having to do speical system intrrupts
    Y2_stepper.processMovement();
    Y3_stepper.processMovement();
    AOAT_stepper.processMovement();
    AOAB_stepper.processMovement();
  }
  Serial.println("Exited While Loop");

  //   if (Trigger_selection == 1) // old external trigger code
  //   {
  //     // LCD External Trigger mode and Serial External Trigger
  //     Serial.println("Steps to move");
  //     Serial.println(movevar[0] * X_mm_to_micro);
  //     X_stepper.setupRelativeMoveInSteps(movevar[0] * 6400); // Future: Make these iun terms of MM
  //     Y0_stepper.setupRelativeMoveInSteps(movevar[1] * 6400);
  //     Y12_stepper.setupRelativeMoveInSteps(movevar[1] * 6400);
  //     Y3_stepper.setupRelativeMoveInSteps(movevar[1] * 6400);
  //     AOAT_stepper.setupRelativeMoveInSteps(movevar[2] / (Degree_per_step[2] / Micro_stepping[2]));
  //     AOAB_stepper.setupRelativeMoveInSteps(movevar[3] / (Degree_per_step[3] / Micro_stepping[3]));
  //     //    E2stepper.setupRelativeMoveInSteps((movevar[*axis*] / Degree_per_step[4]) * Micro_stepping[4]);
  //     //      Serial.print("Waiting in Motion MODE 3: LCD Continous with Trigger"); // Debug Stuff
  //     //     Serial.print("Ready For Trigger");
  //     // digitalWrite(27, HIGH);    // Sound Buzzer That The Control Borad is waiting on user
  //     // delay(10);
  //     // digitalWrite(27, LOW);  // Turn the buzzor onff
  //     while(Go_Pressed =! true){
  //       // do nothing here and wait for the interrupt
  //       delayMicroseconds(1);
  //     }
  //     Go_Pressed = false;
  //     while ((!X_stepper.motionComplete()) || (!Y0_stepper.motionComplete()) || (!Y12_stepper.motionComplete()) || (!Y3_stepper.motionComplete()) || (!AOAT_stepper.motionComplete()) || (!AOAB_stepper.motionComplete()))
  //     {
  //       X_stepper.processMovement();
  //       Y0_stepper.processMovement();
  //       Y12_stepper.processMovement(); // moving the Steppers here was a simple soltuion to having to do system interups and blah blah.
  //       Y3_stepper.processMovement();
  //       AOAT_stepper.processMovement();
  //       AOAB_stepper.processMovement();
  //     }
  //     Abs_pos_error = false;
  //     // return;
  //   }
} // End Function
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

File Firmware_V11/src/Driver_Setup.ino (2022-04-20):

// Driver setup config
#include <TMCStepper.h>
#include <TMCStepper_UTILITY.h>
void DRIVER_SETUP()
{
driverX.beginSerial(115200); // X driver Coms begin
Serial.println("Driver X Enabled\n");
driverX.begin();
driverX.rms_current(1100); // mA
driverX.microsteps(64);
//driverX.en_spreadCycle(0); // Page 44 use stealth chop
driverX.pwm_ofs_auto ();
driverX.pwm_autograd(1);
driverX.pwm_autoscale(1);

driverX2.beginSerial(115200);
Serial.println("Driver X2 Enabled\n");
driverX2.begin();
driverX2.rms_current(1100); // mA
driverX2.microsteps(64);
driverX2.pwm_ofs_auto ();
driverX2.pwm_autograd(1);
driverX2.pwm_autoscale(1);

driverY0.beginSerial(115200);
Serial.println("Driver Y0 Enabled\n");
driverY0.begin();
driverY0.rms_current(1100); // mA
driverY0.microsteps(64);
//driverY0.en_spreadCycle(0);
driverY0.pwm_ofs_auto ();
driverY0.pwm_autoscale(1);
driverY0.pwm_autograd(1);

driverY1.beginSerial(115200);
Serial.println("Driver Y12 Enabled\n");
driverY1.begin();
driverY1.rms_current(900); // mA
driverY1.microsteps(64);
driverY1.pwm_ofs_auto ();

driverY2.beginSerial(115200);
Serial.println("Driver Y12 Enabled\n");
driverY2.begin();
driverY2.rms_current(900); // mA
driverY2.microsteps(64);
driverY2.pwm_ofs_auto ();

driverY3.beginSerial(115200);
Serial.println("Driver Y3 Enabled\n");
driverY3.begin();
driverY3.rms_current(850); // mA
driverY3.microsteps(64);
driverY3.pwm_ofs_auto ();

driverAOAT.beginSerial(115200);
Serial.println("driver e1 enabled\n");
driverAOAT.begin();
driverAOAT.rms_current(900); // ma
driverAOAT.microsteps(64);
driverAOAT.pwm_ofs_auto ();

driverAOAB.beginSerial(115200);
Serial.println("Driver E2 Enabled\n");
driverAOAB.begin();
driverAOAB.rms_current(900); // mA
driverAOAB.microsteps(64);
driverAOAB.pwm_ofs_auto ();

}

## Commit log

2021-10-21 Library Upload & changes to Code for MKS BOARD
2021-10-21 BugFix Serial Dropout Fix
    [Pin_Setup.ino, UI_Functions.ino, UI_Version_10_Port.ino]
2021-11-12 Test Data and GUI Update
    [Test_data.csv, Test_data.xlsx]
2021-11-13 Lead_Screw_Math & Clean_UP
2021-11-13 Fully_Flushed_Gui & Homing_Functions
